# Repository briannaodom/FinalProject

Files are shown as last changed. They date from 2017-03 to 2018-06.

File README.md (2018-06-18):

# Final Project: The Assisted Ab Wheel

### Example Youtube Video of Proper Ab Wheel Usage

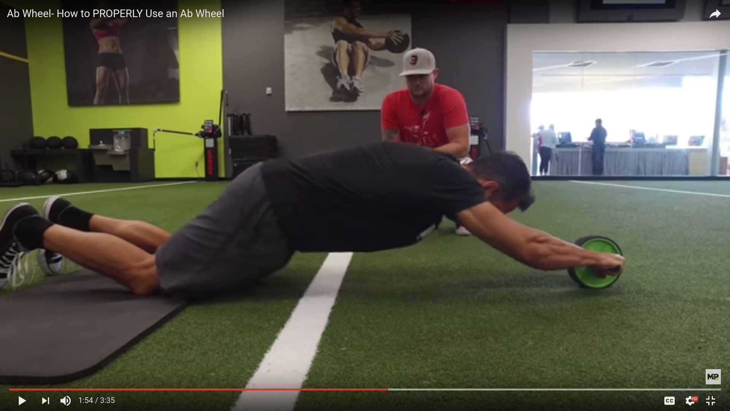
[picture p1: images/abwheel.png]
(https://www.youtube.com/watch?v=rqiTPdK1c_I)


### Goal

Create an Ab Wheel that will have an assisted functionality. The user will roll forward extending the arms and body outward on their knees or in a plank position. Once they have reached maximum extension, they will roll back up to their initial position by pressing a button that will cause the wheel to rotate in the direction that is towards their body. This will allow beginner or out of shape users to build their core muscles. Once a user has achieved an optimal core strength, they can use the Ab Wheel manually.

### Spring Quarter Objectives

1. Computing specs for motor that can handle a load that is dependent on the weight of a user
2. Creating a circuit for hbridge, encoder, and current sensor with Arduino Uno
3. Designing PID controller for current/torque control of the motor
4. Designing a desktop model to simulate a person pushing on an abwheel

More objectives will be added for Summer Quarter at the end of the Spring Quarter

### Supplies

1. Hbridge Driver in this case the DVR8835
2. 2 Potientiometers- one to setup hbridge, one to control LCD lighting
3. LCD to display desired values such as PWM, current, and rotation angle of the motor
4. Battery Pack in this case 6V
5. Encoder Chip
6. Current Sensor Chip
7. DC Motor
8. Arduino Uno

### Componenents

#### LCD 

The LCD currently displays the PWM value that is computed from the analog pin wired to the potientiometer. When the value of the potientiometer increases from 0 to 255, the motor spins quicker in the forward direction and the LCD displays that value.

Useful for LCD and potientiometer setup: 

1. Schematic of LCD and potientiometer [link](https://github.com/briannaodom/FinalProject/blob/master/images/LCD_POT.png)
2. Code for LCD setup [link](https://github.com/briannaodom/FinalProject/blob/master/src/lcdsetup.ino)

#### Hbridge

The hbridge DRV3385 chip is currently wired to drive the DC motor in a forward direction when a button is unpressed and in the reverse direction when a button is being pressed. 

The datasheet to wire the hbridge can be found on the Pololu website [here](https://www.pololu.com/product/2135).

Modifications: VCC wire has been disconnected and the 6V positive wire of the battery goes to VIN. So the hbridge is completely controlled by the the 6V battery and the rest of the circuit by the arduino.

Useful for hbridge and button setup:

1. Schematic of hbridge [link](https://github.com/briannaodom/FinalProject/blob/master/images/hbridge.png)
2. Schematic of button [link]()
3. Code for hbridge setup [link](https://github.com/briannaodom/FinalProject/blob/master/src/hbridgesetup.ino)

#### Current Sensor 

Useful for current sensor setup:

1. Schematic of current sensor [link](https://github.com/briannaodom/FinalProject/blob/master/images/currentsensor.png)
2. Code for current sensor setup [link](https://github.com/briannaodom/FinalProject/blob/master/src/currentsensorsetup.ino)

#### Encoder 

Useful for encoder setup:
1. Schematic of encoder [link](https://github.com/briannaodom/FinalProject/blob/master/images/encoder.png)
2. Code for encoder setup [link](https://github.com/briannaodom/FinalProject/blob/master/src/encodersetup.ino)

#### Youtube Demo of Hbridge Controlling the Motor and LCD Displaying PWM

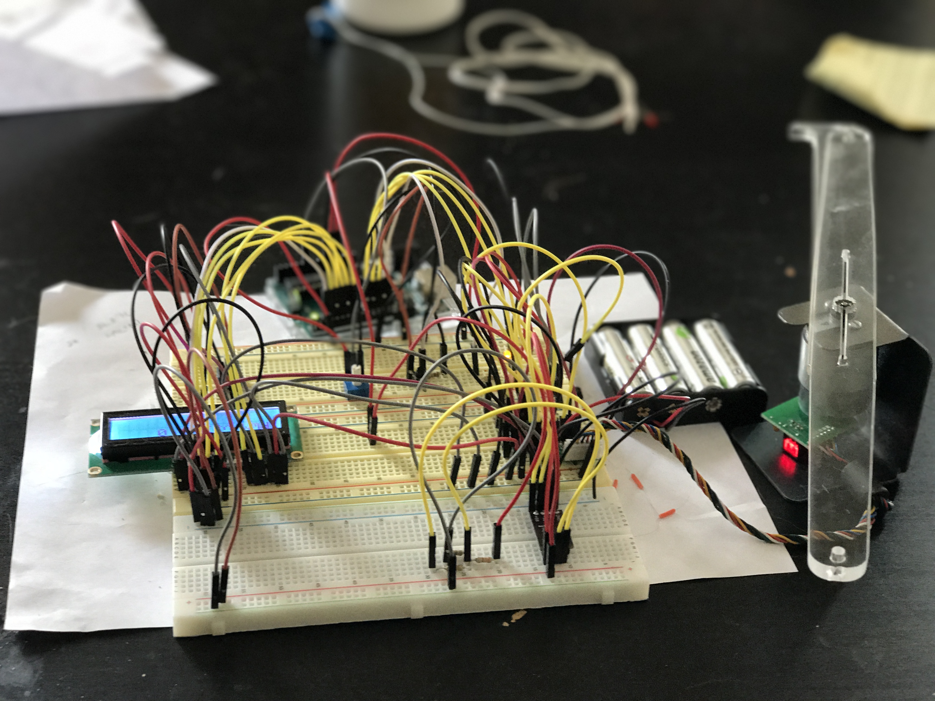
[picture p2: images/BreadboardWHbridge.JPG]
(https://www.youtube.com/watch?v=onr-n5QG-nY&feature=youtu.be)


### Measurements for Desktop Model

Currently taking measurements to build a model of a person in push up position with knees on the ground holding the ab wheel that will be guided by a motor. The measurements have come from my cohort. I'd like to get at least 10-15 subjects before I take an average of each measurement. 

This will have to be redone as the second measurement should be from shoulder to knee. 
For the sake of the desktop model, the third and fourth columns respectfully will have a ration of 1:4, as I did not get these measurements from people in my cohort.

|shoulder to arms  | shoulder to hip | side of hip to side of hip  | side of arm to side of arm
|---|---|---|---|
| 24" | 18" | | |
| 25" | 18" | | |
| 25.5" | 19" | | |
| 27" | 20" | | |
| 27" | 21" | | |
| 26" | 20" | | |
| 24" | 18" | | |

I ended up making the [arm one](https://github.com/briannaodom/FinalProject/blob/master/onShapeDocs/Arm1ForAbWheel.png) and [arm two](https://github.com/briannaodom/FinalProject/blob/master/onShapeDocs/Arm2.png) about 8" with a 6" distance between holes in OnShape. If I ever make a more complex model, I'd use the measurements above or at least a 2:1 or 3:1 ratio between arms and body for the desktop model.

### Measurements for onShape Modeling

Sketch and extrude pictures of all the parts used to build the desktop version of the ab wheel can be found under [OnshapeDocs](https://github.com/briannaodom/FinalProject/tree/master/onShapeDocs)

A future assembly through OnShape will be done showing the whole model put together. However, here is a picture of the current model of my build. The [hub](https://github.com/briannaodom/FinalProject/blob/master/onShapeDocs/HubExtrude.png) is directly attached to the motor and wheel which sits on [slots](https://github.com/briannaodom/FinalProject/blob/master/onShapeDocs/SlotBoxExtrude.png) allowing the motor to move back and forth, when it rotates. 

Due to an error in measurement of the height of the slot box, a second [track](https://github.com/briannaodom/FinalProject/blob/master/onShapeDocs/Track.png) was made with for the wheel to sit on so it is not hovering. I used two extra hubs glued between the tracks to help bridge the distance.

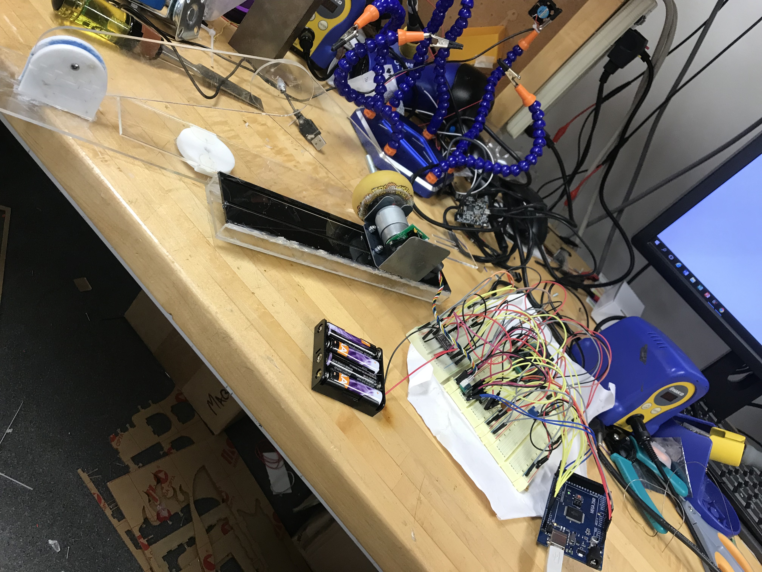
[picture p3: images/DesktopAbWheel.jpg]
[]()

### Current Control 

My main code is [motorandspringsetup](https://github.com/briannaodom/FinalProject/blob/master/src/motorandspringsetup_ino/motorandspringsetup_ino.ino). 

Basically, a potentiometer is hooked up to control k the spring constant. The higher k, the stronger or harder the spring, thus the higher the resistance of the motor. Under the currentController function, we are keeping track of the encoder moving away from 0, the point we want the wheel to be at. Thus our desired current is k times the error of the distance of the motor from its original starting position. 

Next, a second error is calculated which is the error between the desired current and the actual current being measured from the motor with the current sensor. PD gains are given to get the motor to add resistance and keep the wheel in line in the CW direction of the rotation of the motor, which calculates a new pwm value that is sent to the motor. Anti-windup limits the new pwm values. 

### Issues/Limitations

The current motor I am using could only go up to 11V, thus even at the highest voltage and with two bolts holding the motor down in the slots, the motor had a hard time being moved. Thus, it was hard to figure out the proper gains for the PID of the [currentcontroller](https://github.com/briannaodom/FinalProject/blob/master/src/motorandspringsetup_ino/motorandspringsetup_ino.ino).

Therefore, for now, I provided a link to a video that shows the wheel moving in a CW rotation, 
which is basically the wheel trying to go back to 0. A little oscillation at the end of the wheel rotating occurs, so a higher or better derivative gain needs to be found. [vimeo](https://tinyurl.com/AbWheelSpin)  

For now, a motor that can provide a higher torque needs to be bought for the desktop model.

Lastly, two interrupts would have been nice to use for the encoder counts to have a better resolution. I tried using pins 2 and 3 on the arduino, but using two at a time caused an issue. Would have to do more research to figure out how to use both. 

### Future Goals

Fine tune the PD gains better with matlab, as what I currently have is by eye. 

Do measurements for a motor that would provide enough torque to handle a human body.

Create a new circuit and design a pcb board that includes an on/off switch.

Create a bigger model in onshape and buy the parts to put it all together.

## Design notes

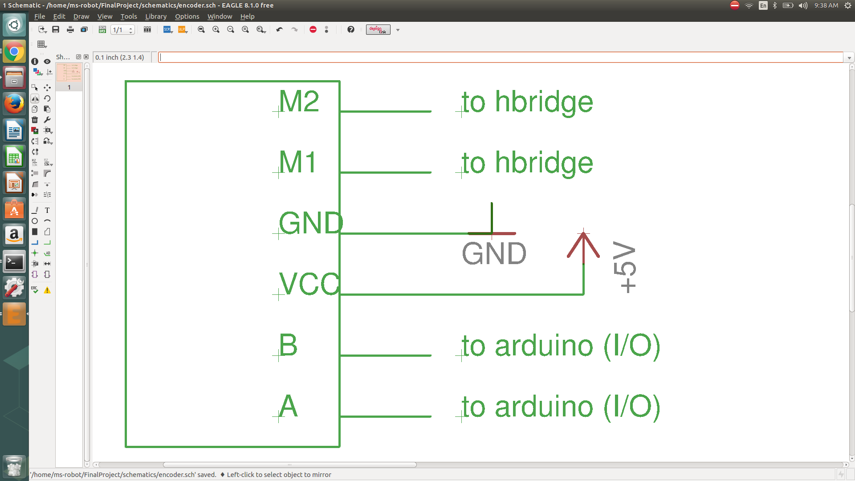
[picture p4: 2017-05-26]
images/encoder.png

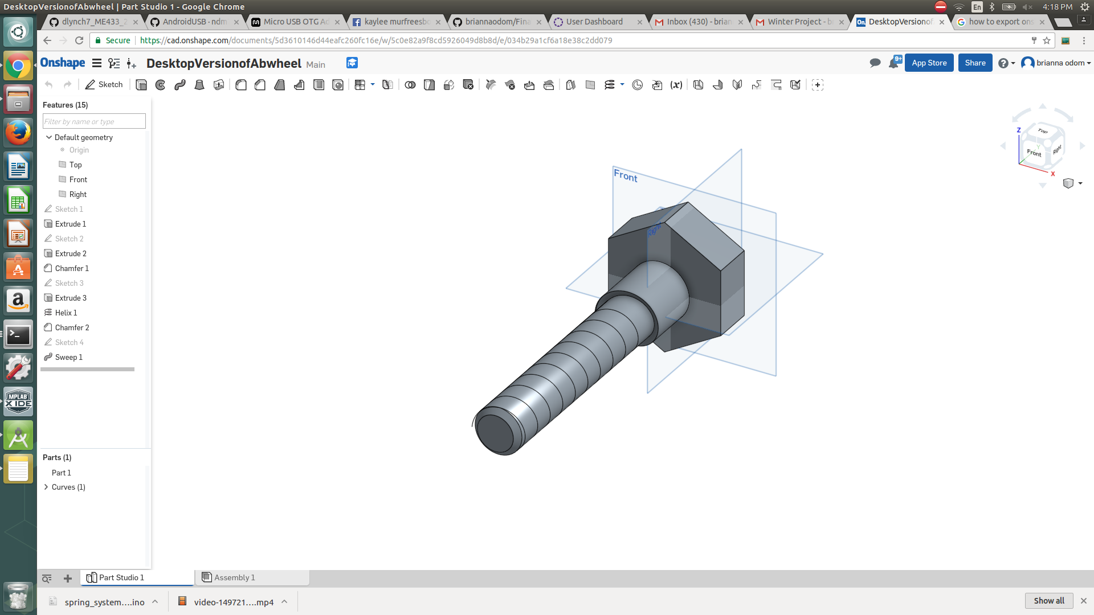
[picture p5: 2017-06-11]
images/bolt.png

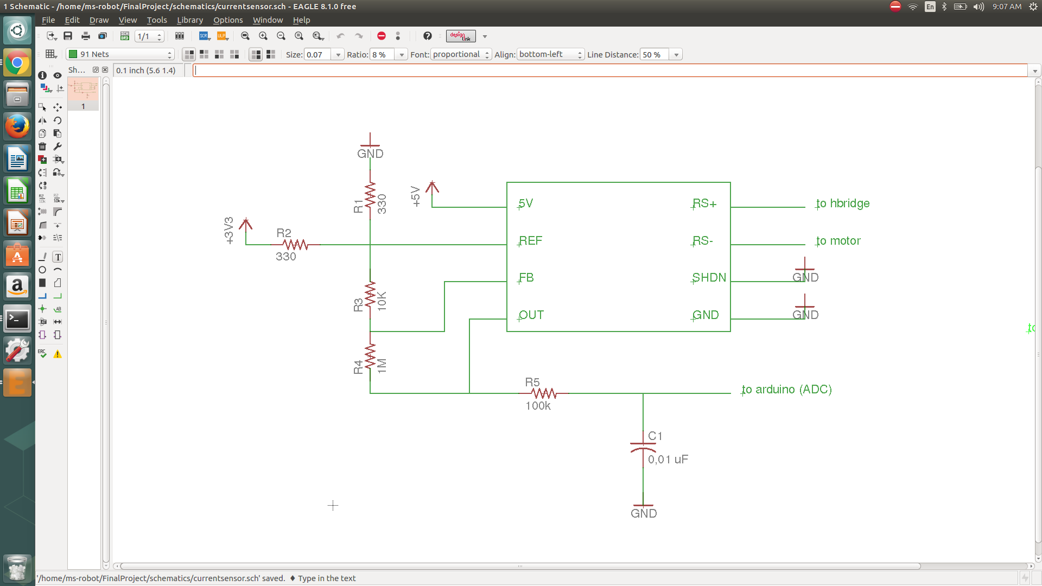
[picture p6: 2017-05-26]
images/currentsensor.png

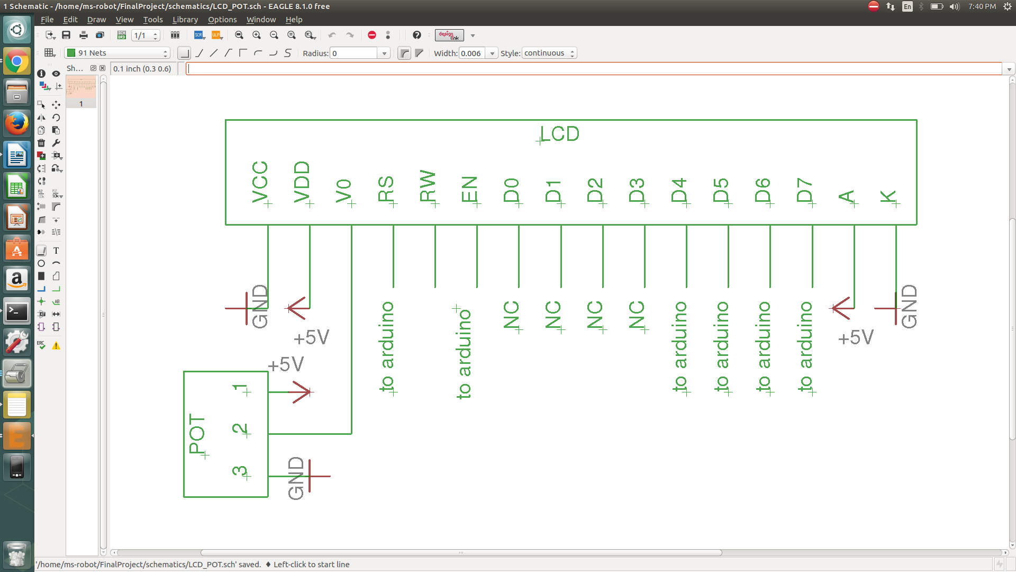
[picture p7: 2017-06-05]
images/LCD_POT.png

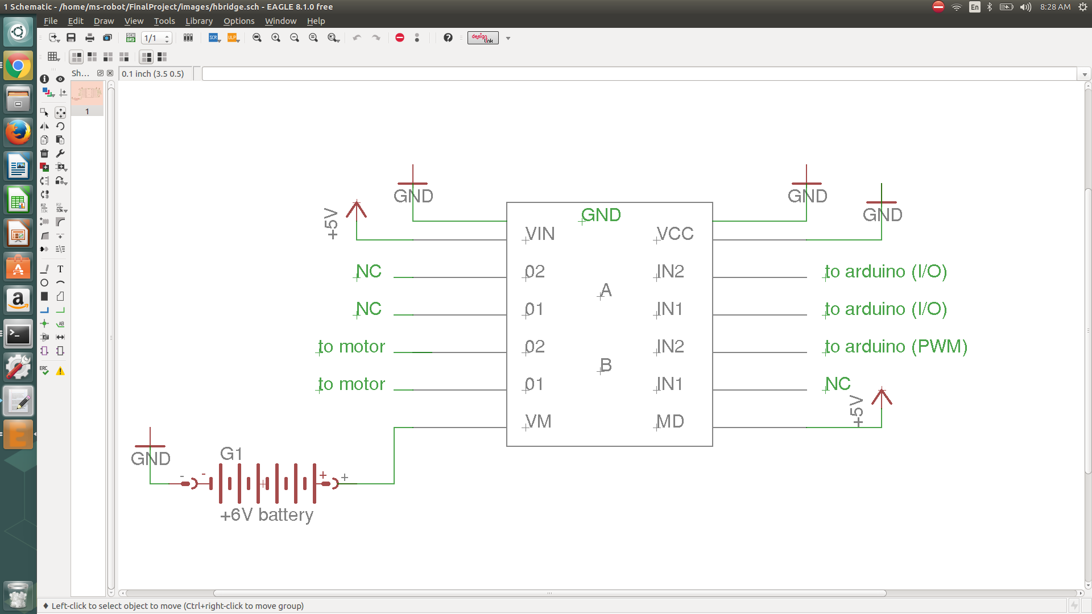
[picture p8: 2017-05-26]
images/hbridge.png

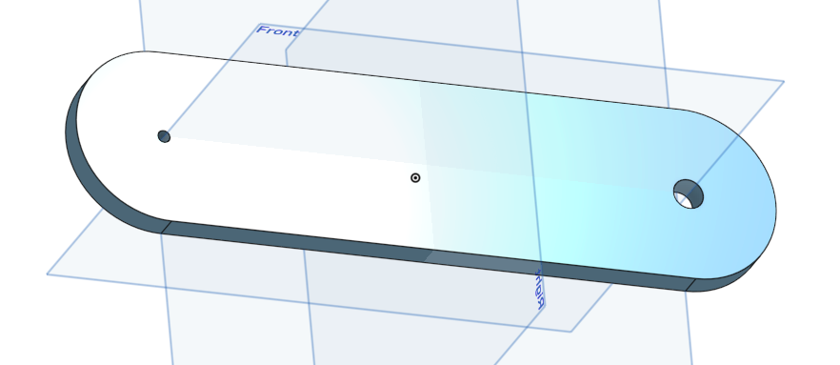
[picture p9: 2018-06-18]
onShapeDocs/Arm2Extrude.png

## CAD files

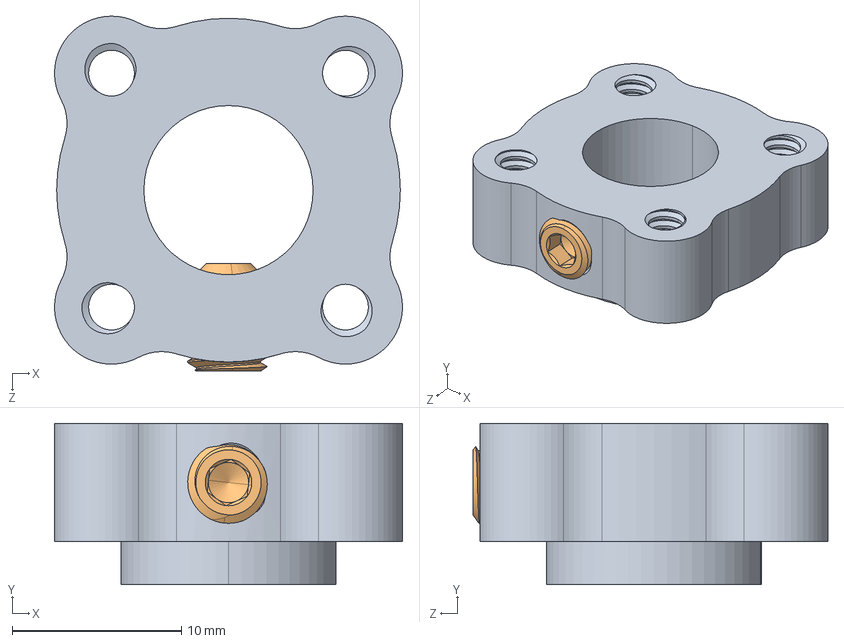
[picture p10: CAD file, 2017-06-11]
onShapeDocs/545640 assembly.STEP
20.6 x 9.53 x 21.0 mm
632138_91375A438

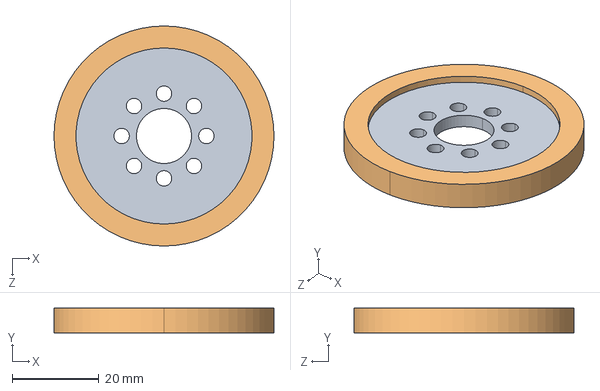
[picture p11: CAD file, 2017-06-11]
onShapeDocs/595711 assembly.STEP
50.8 x 5.71 x 50.8 mm
595711 wheel
636102 for 2in precision disk wheel

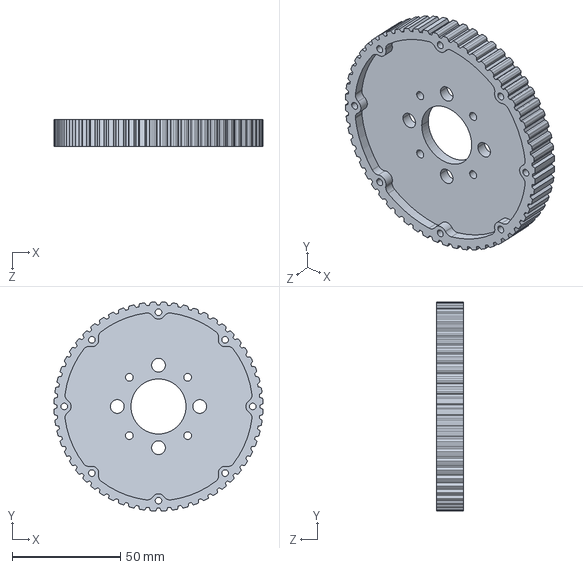
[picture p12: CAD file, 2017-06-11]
onShapeDocs/615394.STEP
96.5 x 96.5 x 12.7 mm

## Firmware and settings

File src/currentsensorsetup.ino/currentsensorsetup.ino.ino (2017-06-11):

const int currentAnalog = A1;  //analog pin to get current
const int pwm = 11;            //pwm pin set to 11
const int in2 = 9;             //hbridge pin 
const int in1 = 10;            //hbridge pin
const int encoderPinA = 1;     //encoder A pin
const int encoderPinB = 8;     //encoder B pin 
volatile int encoderPos = 0;   
int prevEncoderPos = 0;    
int sensorVal;
float voltage;
int error;
int dError;
int desiredCurrent;
int measCurrent;
int eint;
int eprev;
int prevPWM; 
int propGain;
int integralGain;
int derivGain;
int PIDval = 65;        
int FALSE = 0; 
int stopAb;
int torque;
int prevTorque;
void incCurrent();
int getCurrent(int sensorVal);
void getEncoder();

void setup() {
  pinMode(currentAnalog, OUTPUT);
  pinMode(pwm, OUTPUT);
  pinMode(in1, OUTPUT);
  pinMode(in2, OUTPUT);
  Serial.begin(9600);
  analogWrite(pwm, 0);                   //motor at rest (0% duty)

  digitalWrite(encoderPinA, HIGH);       //interrupt
  digitalWrite(encoderPinB, HIGH);
  attachInterrupt(0, getEncoder, CHANGE);

}

void loop() {
 getVoltage();
 if (checkEncoder == 1){
   desiredCurrent = slope*encoderPos;     //spring
 }
 checkEncoder != checkEncoder;

}

void incCurrent(){
   error = desiredCurrent - measCurrent;   //proportional gain
 
   if (error <= 0.01 || error >= 0.01) {
    dError = error - errorPrev;
    eint = eint + error; 
    newCurrent = propGain * error;
    eprev = error;
    voltOfMotor = newCurrent/2;
    newCurrent = PWMprev + voltOfMotor*255;
    PWMprev = newCurrent;

    if (newCurrent < -255){               //add limits
      newCurrent = -255;
    }
    else if (newCurrent > 255){
      newCurrent = 255;
    }

    if (torque > //someval) {
      stopAb != FALSE; 
   }
    if (stopAb) {
      analogWrite(pwm, 0);                //abwheel stops
    }
    else if (newCurrent >= 0){
      digitalWrite(in1, LOW);
      analogWrite(pwm, newCurrent);
    }
    else {
      digitalWrite(in1, HIGH);
      newCurrent = -newCurrent;
      analogWrite(pwm, newCurrent);
    }
}

//will write more safeties and have to figure out torque equations 
//(sum of moments * acceleration)

void getCurrent(int PIDval){
  sensorVal = analogRead(currentAnalog);  //read analog
   voltage = 5*(sensorVal/1023);           //convert analog val (0-1023) to voltage (0V-5V);
  //Serial.println(sensorVal); 
   Serial.println(voltage);                //print voltage
   current = (voltage/PIDval-2.5/PIDval)*(1/0.015);
   return current;
}

void getEncoder(){
  encoderAState = digitalRead(encoderPinA);           //read encoder A pin
  if (encoderAState != encoderAPrevState){            //check current to prev state
    if (digitalRead(encoderPinB) != encoderAState){   //check encoder A and B are different
      counter++;                                      //increment counter 
      angle ++;                                       //increment angle (clockwise)
    }
    else{                                             //encoder A and B same
      counter--;                                      //deincrement counter
      angle--;                                        //deincrement angle (counterclockwise)
    }
    if (counter >=30){                                //setting limits for incrementing
      counter = 0;
  }
  encoderAPrevState = encoderAState;                  //make previous state the current state before going thru again
 }
}

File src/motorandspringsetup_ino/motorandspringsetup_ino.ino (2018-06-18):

#include <LiquidCrystal.h>


const int encoderPinA = 3;              //encoder interrupt pin for encoder A
const int encoderPinB = 2;              //encoder interrupt pin for encoder B
const int POT = A0;                     //potientiometer for controlling spring constant
const int in2 = 10;                     //not needed 
const int in1 = 9;                      //input pin for motor direction
const int pwm = 11;                     //pwm pin for motor
int ADCval;                             //for pot
int ADCval2;                            //for voltage
float current;
float voltage;    
float error;                            //following few terms for PID
float error1;
float e_int = 0;
float e_int1 = 0;
float prev_error = 0;
float new_current;
float new_position;
float motorVoltage;
float d_error = 0;
float voltage2;
int new_PWM = 0;
int prev_PWM = 0;
int k;                                   //spring constant
//int TurnOffMotor = 0;
volatile long encoderPos = 0;
int angle = 0;
int aPinState;                           //states of encoder pins A and B
int bPinState;                              
int currentPin = A1; 
int desiredCurrent;
int desiredEncoderPos;                  
float voltVal;
int Prop_gain = 1;
int d_gain = 0.1;
int currentGain = 100;                   //gain that affects range of current
int motorState = HIGH;                   //current state of output pin;
LiquidCrystal lcd(8,7,6,5,20,21);        //lcd pin setup


int setValueOfK(int POT){                //setting up potientiometer for spring constant that will be increased for higher resistance
  ADCval = analogRead(POT);
  k = map(ADCval, 0, 1023, 0, 10);
  return k; 
}


void rotateCW(){                             //following method of direction
  digitalWrite(in1, LOW);              
  digitalWrite(in2, HIGH);
  //delay(100);  
}

void rotateCCW(){                    
  digitalWrite(in1, HIGH);
  digitalWrite(in2, LOW); 
  //delay(100); 
}

void STOP(){                        
  digitalWrite(in1, HIGH);
  digitalWrite(in2, HIGH); 
  delay(100);  
}

void encoder(){
  aPinState = digitalRead(encoderPinA);
  bPinState = digitalRead(encoderPinB);  
  if (bPinState != aPinState ) {        //rotating clockwise if diff        counter = -counter;
    encoderPos ++;
  }
  else {
    encoderPos --;                     //rotating counterclockwise
  }
}

void encoder2(){                        //not being used since two interrupts weren't working
  aPinState = digitalRead(encoderPinA);
  bPinState = digitalRead(encoderPinB);  
  if (bPinState != aPinState ) {         //rotating clockwise if diff        counter = -counter;
    encoderPos ++;
  }
  else {
    encoderPos --;                     //rotating counterclockwise
  }
}

int calculateCurrent(int voltVal){                      //function for calculating current from voltage
  ADCval2 = analogRead(currentPin);
  voltage = 5000*(ADCval2/1024.0);                      //gives mV, https://circuits4you.com/2016/05/13/arduino-asc712-current/
  current = (voltage-512.0)/(currentGain*0.015);          //2.5 ACSoffset, 512 same as 2.5V, 1.5 = currentGain * 0.015 (value of resistor)
  // lcd.clear();
  //lcd.print(String("ADC:") + String(ADCval2));
  //lcd.setCursor(0,1);
  //lcd.print(String("voltage:"));
  //lcd.setCursor(9,1);
  //lcd.print(voltage);
  //lcd.setCursor(0,0);
  // lcd.print("curr:");

  // lcd.print(current);

  return current;
}

void currentController(){
  desiredEncoderPos = 0;                                 //desired position for motor to roll back to
  error = desiredEncoderPos - encoderPos;                //trying to get wheel to spin back to 0, as user pushes on it
  desiredCurrent = k*error; 
  // lcd.setCursor(6,0);
  // lcd.print("dC:");
  // lcd.print(desiredCurrent);
  error1 = desiredCurrent-current;                       //PID controller
  // lcd.setCursor(12,1);                        
  // lcd.print(error);

  //if (error1 <= -0.025 || error1 >= 0.025)
  d_error = error - prev_error;
  new_current = Prop_gain*error + d_gain*d_error;          //figure out prop gain
  //prev_error = error;
  //voltage2 = new_current/185.0;                         //185 mV/A, 1 for 20A Module, .66 for 30A Module
  new_PWM = new_current;//prev_PWM + voltage2*255.0;  
  lcd.setCursor(0,1);
  lcd.print(new_PWM);   
  prev_PWM = new_PWM;

  if (new_PWM > 255 ){
    new_PWM = 255;
  }
  else if (new_PWM < -255){
    new_PWM = -255;
  }
  
  if (new_PWM >= 0) {
    rotateCW();
    analogWrite(pwm, new_PWM);
  }
  else {
    rotateCCW();
    analogWrite(pwm, -new_PWM);
  }
}  


void setup() {
  Serial.begin(9600);
  pinMode(pwm, OUTPUT);
  pinMode(in1, OUTPUT);   //for control of hbridge
  pinMode(in2, OUTPUT);
  pinMode(encoderPinA, INPUT);
  pinMode(encoderPinB, INPUT);
  lcd.begin(16,2);
  digitalWrite(in1, motorState);
  digitalWrite(in2, motorState);            //set initial motor state
  attachInterrupt(0, encoder, CHANGE);     //interrupt for encoder, 0 is for digital pin 2
  //attachInterrupt(1, encoder2, CHANGE);     //1 is for digital pin 3, if we want more resolution. having issues with 2 however
}

void loop() {
  lcd.clear();
  lcd.setCursor(0,0);
  lcd.print("encoder: ");
  lcd.print(encoderPos);
  k = setValueOfK(POT);                  //spring constant for spring equation
  //lcd.setCursor(0,0);
  //lcd.print(String("k:") + String(k));
  current = calculateCurrent(voltVal);
  //lcd.setCursor(0,1);
  //lcd.print("curr:");
  //lcd.print(current);
  currentController();
  //analogWrite(pwm,200);
  //rotateCCW(); 
  //STOP();
  //rotateCW();
}

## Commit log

2017-03-31 added image of ab wheel
2017-04-12 added image of circuit diagram for PIC32
2017-04-12 added image of schematic used for PCB
2017-04-12 added layout of breadboard that follows circuit diagram for PIC32
2017-04-12 added library being used to build PCB
2017-04-12 added schematic that has components being used to design PCB for pic32
    [me433_2017.sch]
2017-05-01 added arduino code to test LED light
2017-05-02 added code for push button
2017-05-02 added debounce function for push button
2017-05-02 added code to pring ADC valueto the LCD fro the potientiometer
2017-05-22 deleted images, schematics, and code for PIC i will not be using
    [me433_2017.sch]
2017-05-22 added img of current circuit with hrbdige wired and current sensor being wired. also added demo of control of motore with pwm and hdbridge
2017-05-24 testing voltage with POT
2017-05-24 setting up current sensor chip
2017-05-24 added information on current sensor
2017-05-24 added encoder code and edited current sensor code
2017-05-24 added encoder code link
2017-05-26 added schematic for hbridge
    [hbridge.sch]
2017-05-26 added hbridge schematic to schematic folder and added an image in image folder
    [hbridge.sch]
2017-05-26 put in link to hbridge schematic
2017-05-26 added pic of current sensor sschematic
2017-05-26 added schematic code to folder for eagle
    [currentsensor.sch]
2017-05-26 added link to current sensor image
2017-05-26 added encoder image of schematic
    [currentsensor.sch]
2017-05-26 added schematic for encoder into folder
    [encoder.sch]
2017-05-26 added link to encoder schematic
2017-05-31 added encoder function to main to get degrees of rotation
2017-05-31 updated encoder code
2017-06-05 saved the schematic file for the LCD/POT
    [LCD_POT.sch]
2017-06-05 added link for LCD/POT schematic and added html code for youtube video
2017-06-11 updated current sensor code
2017-06-11 added image of bolt from onShape created
2017-06-11 added source files from servocity of parts measured for onShape design
    [545640 assembly.STEP, 595711 assembly.STEP, 615394.STEP]
2018-06-10 hbridge wires fixed. spinds again
    [hbridgesetup.ino]
2018-06-10 changed pins for lcd to work on arduino mego. interrupt pins now 20 and 21
2018-06-10 encoder works. positive counts clockwise and vice versa
2018-06-10 encoder correctly counts with hand churn but not by analog write. working on current sensor
    [motorandspringsetup_ino.ino]
2018-06-12 motor encoder works now with analog write. changed variable from into to float
2018-06-12 current sensor displaying correct voltage and current
    [motorandspringsetup_ino.ino]
2018-06-13 working on setting up PID controller and attaching 2 interrupts
2018-06-15 fixed circuit where vcc goes to nothing and hbridge is powered by battery. Stop actually stops now
    [motorandspringsetup_ino.ino]
2018-06-16 fixed PID controller for current. Working on tuning gains.
    [motorandspringsetup_ino.ino]
2018-06-18 added the onshape sketches and extrudes for ab wheel
2018-06-18 added pic of Desktop ad wheel built with circuit
2018-06-18 added modification to circuitfor hbridge and added link to vimeo video for ab wheel spinning in current state with PID
2018-06-18 added limitations with regards to the interrupts for the encoder
